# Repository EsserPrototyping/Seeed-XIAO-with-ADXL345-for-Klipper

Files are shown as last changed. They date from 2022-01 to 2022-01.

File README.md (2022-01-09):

# Seeed-XIAO-with-ADXL345-for-Klipper
This will use the Seeed XIAO MCU instead of the RPI for Input Shaper measurements, so it can be connected to different PI's via USB.

I had trouble getting my ADXL345 to run directly on the PI with longer cables (SPI does not like long wires).
With the XIAO as MCU, longer USB cables can be used and the connection to the ADXL is way shorter.

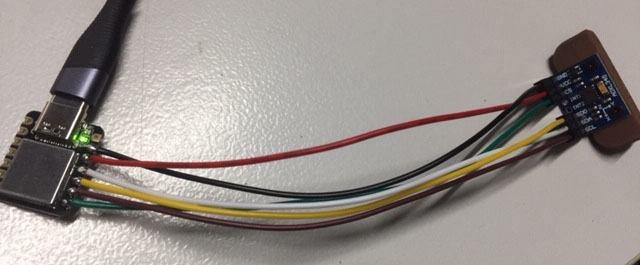
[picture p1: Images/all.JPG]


# Klipper ADXL installation:

Original instructions... https://www.klipper3d.org/Measuring_Resonances.html

If you already configured Input Shaper with your PI, you can skip this part.

- Via Putty:
```
~/klippy-env/bin/pip install -v numpy
sudo apt update
sudo apt install python3-numpy python3-matplotlib
```
..instead of the PI as MCU, we will configure the XIAO
___________________________________________________

# Configure the MCU - Seeeduino XIAO

Original instructions... https://github.com/Tircown/ERCF-easy-brd

- Install bossac (version =1.8):
```
sudo apt install libreadline-dev libwxgtk3.0-*
git clone https://github.com/shumatech/BOSSA.git
cd BOSSA
make
sudo cp bin/bossac /usr/local/bin
```
- Prepare the firmware:
```
cd ~/klipper
make menuconfig
```
___________________________________________________
- uncheck extra low-level options
- Architecture: SAMD21/SAMD51
- Processor: SAMD21G18 (Arduino Zero)
- Clock: Internal clock
- Bottloader offset: 8KiB bootloader (Arduino Zero)
- Communication: USB
___________________________________________________

```
make clean
make
```
___________________________________________________

- Short reset two times on Xiao ( orange led on )

More informations on how to reset for flashing:
https://wiki.seeedstudio.com/Seeeduino-XIAO/#enter-bootloader-mode

- Flash XIAO via Putty:
```
sudo /usr/local/bin/bossac -i -d -p /dev/ttyACM1 -e -w -v -R --offset=0x2000 out/klipper.bin
```
- Reboot PI...
___________________________________________________

- Get serial port via Putty:
```
ls /dev/serial/by-id/*
```
Should be something like this: /dev/serial/by-id/usb-Klipper_samd21g18a_96FA56235136575020312E30142D15FF-if00

- Copy it for the printer config
___________________________________________________

# Edit printer.cfg:
- Change the serial to what you´ve received in the previous step.
```
[mcu xiao]
serial: /dev/serial/by-id/usb-Klipper_samd21g18a_96FA56235136575020312E30142D15FF-if00

[samd_sercom my_sercom]
sercom: sercom0
tx_pin: xiao:PA6
rx_pin: xiao:PA5
clk_pin: xiao:PA7

[adxl345]
cs_pin: xiao:PB9

[resonance_tester]
accel_chip: adxl345
probe_points:
   55,55,20
```
___________________________________________________

# XIAO hardware connection:

| XIAO | ADXL |
|---|---|
| GND	| GND |
| 3V | VCC |
| 10 (MOSI) | SDA |
| 9 (MISO) | SDO |
| 8 (SCK) | SCL |
| 7 (CS) | CS | 

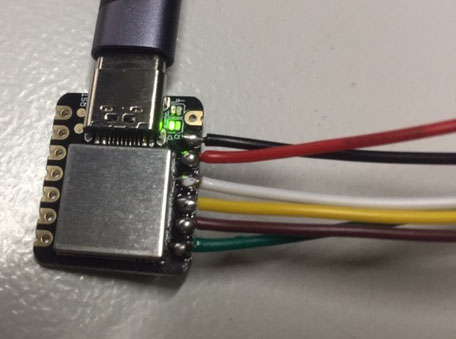
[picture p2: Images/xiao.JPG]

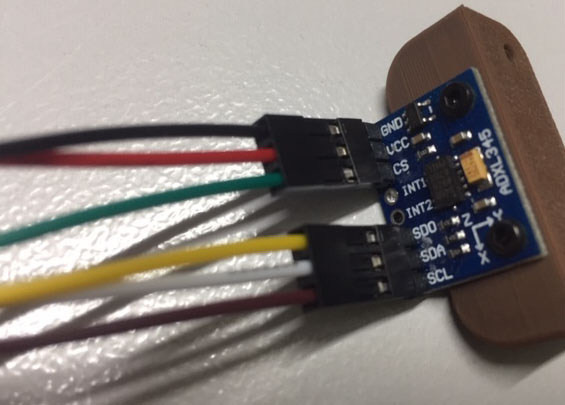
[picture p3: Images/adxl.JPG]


# Print the case for the XIAO if you want to:
https://github.com/EsserPrototyping/Seeed-XIAO-with-ADXL345-for-Klipper/tree/main/XIAO_Case_3D

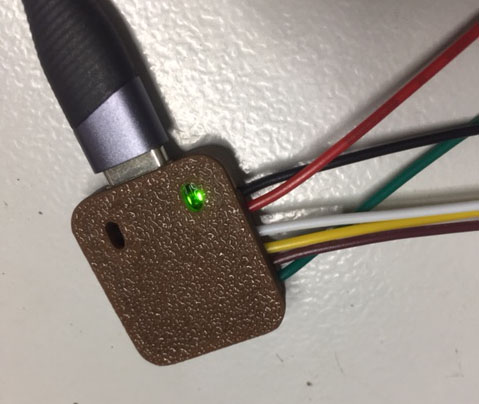
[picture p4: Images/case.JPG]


___________________________________________________
# Use it as described here:
https://www.klipper3d.org/Measuring_Resonances.html#measuring-the-resonances
- If you´re using it with different printers, just uncomment the part from the printer.cfg, so mainsail will not throw an error if the XIAO is not connected.

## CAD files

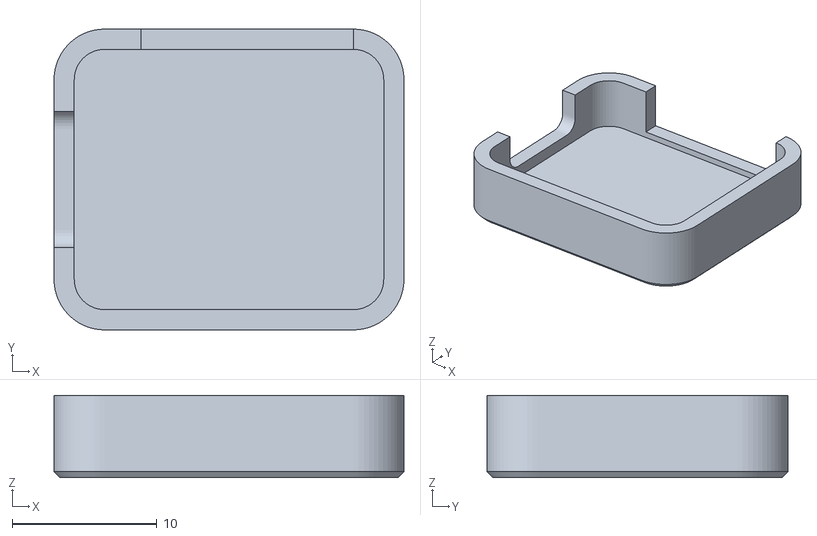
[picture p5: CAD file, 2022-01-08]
XIAO_Case_3D/XIAO_Case_bottom.stl
24.2 x 20.8 x 5.67

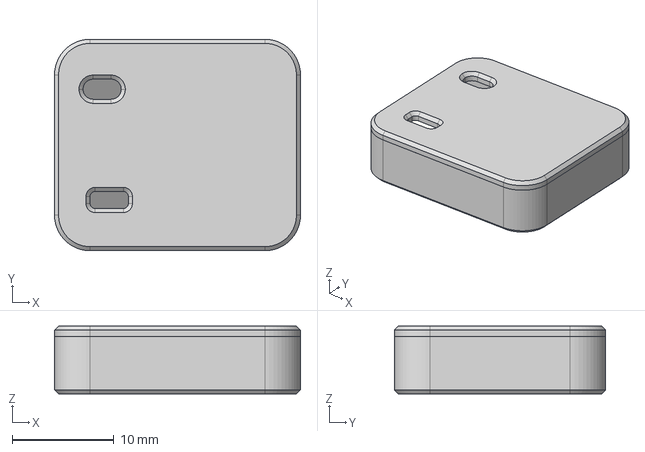
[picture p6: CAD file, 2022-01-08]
XIAO_Case_3D/XIAO_Case.step
24.2 x 20.8 x 6.67 mm

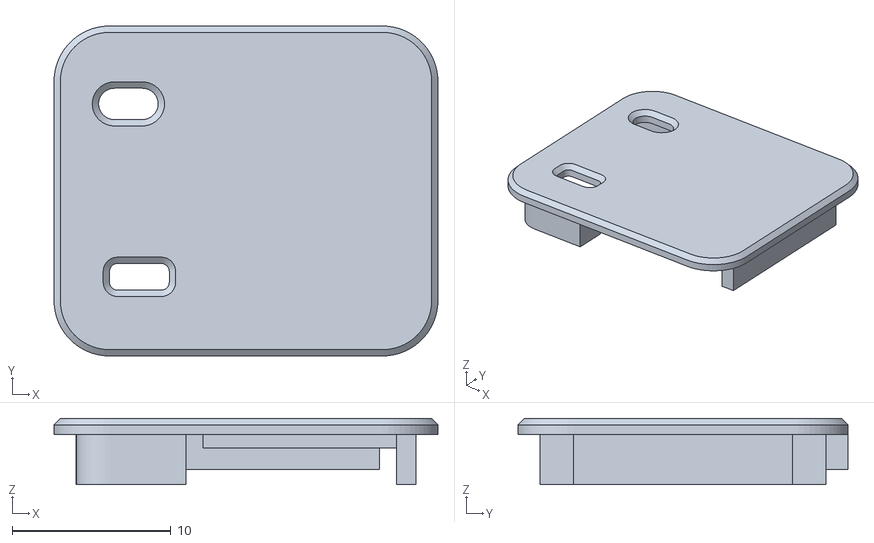
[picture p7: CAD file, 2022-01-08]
XIAO_Case_3D/XIAO_Case_top.stl
24.2 x 20.8 x 4.17
